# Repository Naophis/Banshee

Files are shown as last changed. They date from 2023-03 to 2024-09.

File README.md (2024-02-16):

# Banshee
 
2022年全日本大会で突貫で2セル化したExiaSnowWhiteをベースに、正式な2セル機として作成したシリーズ。  
ExiaSnowWhiteでは電源周りのノイズに苦戦した反省から回路の見直しを実施。  
足回りについてはマイクロマウス合宿で発表した「ベアリングホルダー方式」を採用することで、足回りの剛性を強化。高速走行時の安定性につなぐことができた機体です。

このリポジトリでは、Bansheeで利用しているすべてのソースコードと基板のファイルを公開しています。

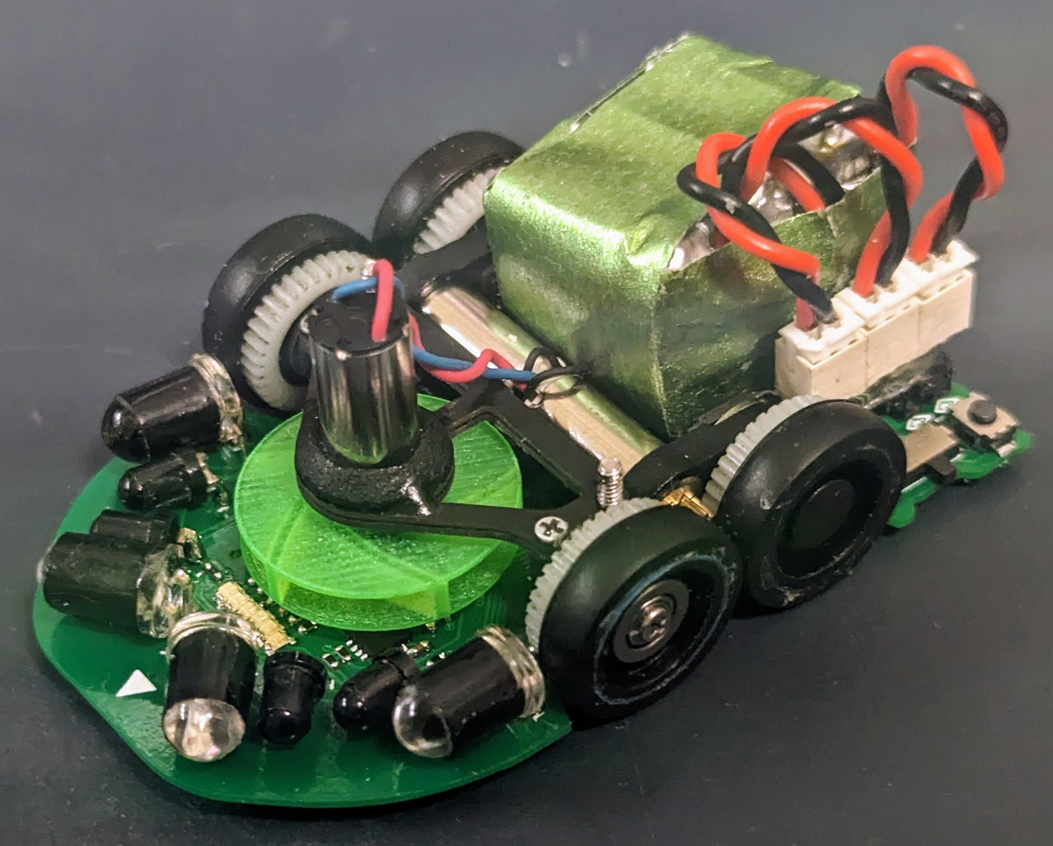
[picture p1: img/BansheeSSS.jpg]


## 利用部品解説

### 1. CPU
ESP32-S3の以下の型番を利用
* ESP32-S3-FH4R2 (Banshee/BansheeAlter)
* ESP32-S3-PICO-1 (Banshee.SSS)

上記の2モデルは昨年発売されておらず、今シーズンから採用。  
昨年使用していたESP32-S3-FN8との違いはPSRAMが搭載で、2MBまでログを取得できるようになったことで細かい解析ができるようになった。

ESP32-PICO-1ではオシレーターの内蔵版となったことで部品点数削減につながった。

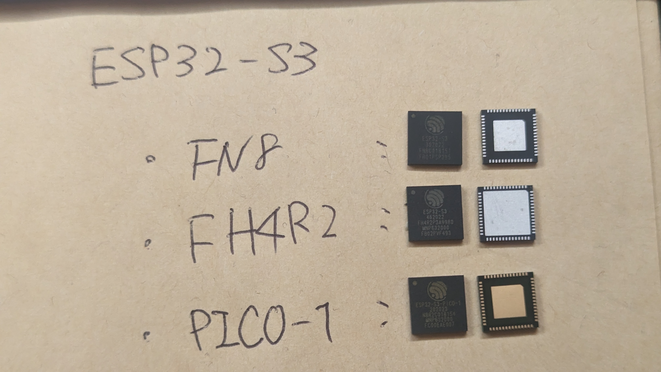
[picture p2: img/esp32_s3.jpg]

画像の通りパッドに違いがある。

#### 1.1 困ったこと
#### 1.1.1 FreeRTOSの固着
ESP32-S3ではデータシートにオシレーターの推奨回路が提示されているが、そのとおり実装すると、モーターを高Dutyで回した際に、FreeRTOSが停止するという問題が発生、推奨回路のコンデンサを除去することで解決した。

#### 1.1.2 データシートにないピンの初期値High問題
書き込み時、電源投入時にHighを出力するピンが存在した。  
ESP32の他シリーズではデータシートに記載しているものもあるがS3では未記載である。
モータードライバにつながったピンに利用すると書き込み時にDuty100%で回転するなど、運用面の問題が発生するため回路の作り直しにつながった。

以下が問題のピン
* PIN26: GPIO20
* PIN28: GPIO26
* PIN44: GPIO39
> 他にもある可能性があり。

### 2. MotorDriver
* DRV8835  (Banshee/BansheeAlter)
* TB6614FNG (Banshee.SSS)

#### 2.1 DRV8835
多くの機体で採用されているが、その理由は以下の通り。
1. 小型ながら2A出力できるため、パフォーマンスが高い。
2. 内部抵抗が300mΩと低い
3. スイッチング周波数が最大250kHzと高く、モーターの特性に対応しやすい。
4. dead timeが100nsecと短いため、高めのPWM周波数に対応しやすい。
dead timeについては、大きい場合High-Lowの切り替えに時間がかかりすぎ、何も出力できないということがあり得る。同社の別のモータードライバでは同じような使い方をするとモーターが回らないということがあり得る。

しかし、最大定格が12Vまでであることから、3セルには対応できないため、TB6614FNGに切り替えた。

### 2.2 TB6614GNG
ディスコン部品であり、パッケージもSOP16と大きいが採用理由は以下の通り。
1. 定格が15Vと3セルに対応
2. 出力が瞬間最大4.5Aまで出力できる
3. スイッチング周波数が400kHzと非常に高く、モーターの特性に対応しやすい
4. dead timeが80nsecと短い

3セル化に伴い、クラシックで利用実績があったICであり、パワー勝負するために信頼できることから採用した。

### 3. PowerSupply
#### 3.1 LXDC55
2セル、3セルから直接3.3Vを取得する場合損失が大きく、熱による影響と効率の観点からDCDCコンバータを採用。入力側に容量が大きいコンデンサをつけないとノイズが乗りやすいため、高分子タンタルコンデンサを複数搭載することでノイズ問題は解決した。

> 約4.2Vを出力するよう、500Ωを利用。  

秋月にて購入できるため採用。

#### 3.2 MIC5319-3.3YM5
3.3V出力に利用。LEDの出力を大きくしたため、500mA出力できるこのICを採用。
データシート通りバイパス用のピンに470pFのコンデンサをつけることでノイズの低減効果がある。

秋月にて購入できるため採用。

### 4. LED + PhotoTransistor
* LED:
  * OSI5FU3A11C
  * VSLY5940
* PhotoTransistor: 
  * LTR-4206E

BCR421UFD（定電流回路）を使うことで安定したセンシングを狙っていたが、
昨年の全日本大会では会場の照明が近いことから、環境ノイズの影響を大きく受けた。  
今年も同じ会場になることから、SN比が良くなるよう、高出力化できる＋LTR-4206Eの帯域に合う大型LEDを採用した

#### 5. gyro
LSM6DSRXTRを採用。4000deg/sec対応している点、昨年のExiaSnowWhiteから継続採用

#### 6. encoder
AS5147Pを採用。14bit対応+28000RPMまで対応しているため継続採用。

ベアリングホルダー方式ではエンコーダ基板に穴を開けることで位置決めしやすいした。

## システム解説

Espressif社がESP32向けにカスタムしたFreeRTOSを利用。  
マイクロマウスでは一定周期で実行したい処理と非同期で実行したい処理が大きく分かれる、これらが混在すると周期に乱れが生じてしまう。ESP32-S3はCPUを2コア搭載していることから、物理的に分けて処理することでシステム全体を滞りなく動かすことを狙った設計となっている。
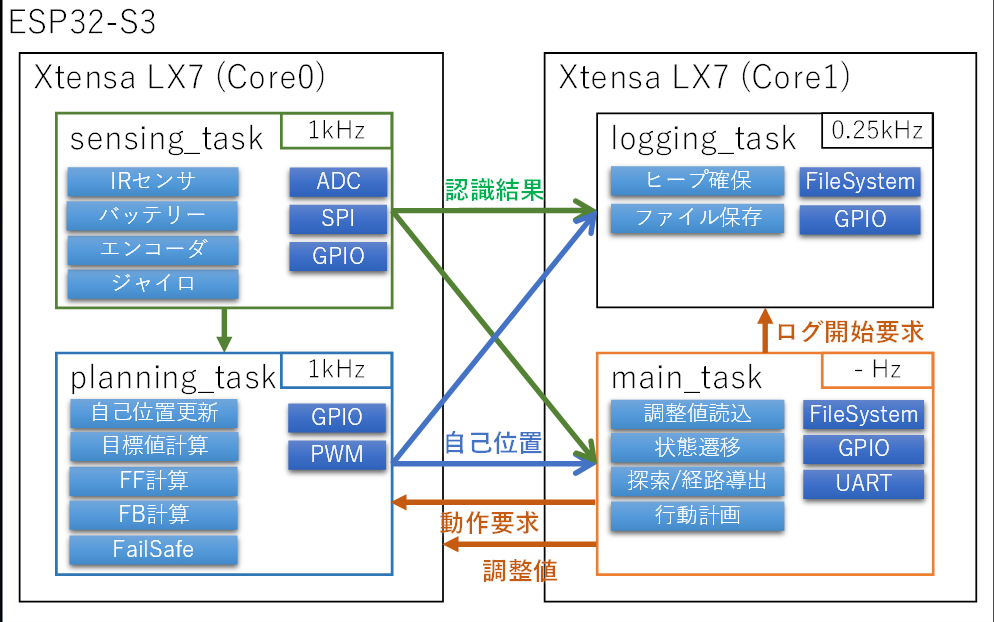
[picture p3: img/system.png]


### 工夫
リアルタイムOSを利用しているとはいえ、タスクの優先順位次第では一定周期で処理できないことがある。特にエンコーダは前回値との差を使い速度を算出するため時刻差の影響を大きく受けた。

対策として、前回取得した時刻を記憶、現在時刻との差分から速度、距離の算出に利用したことで制御・判断の精度向上した。

### 課題
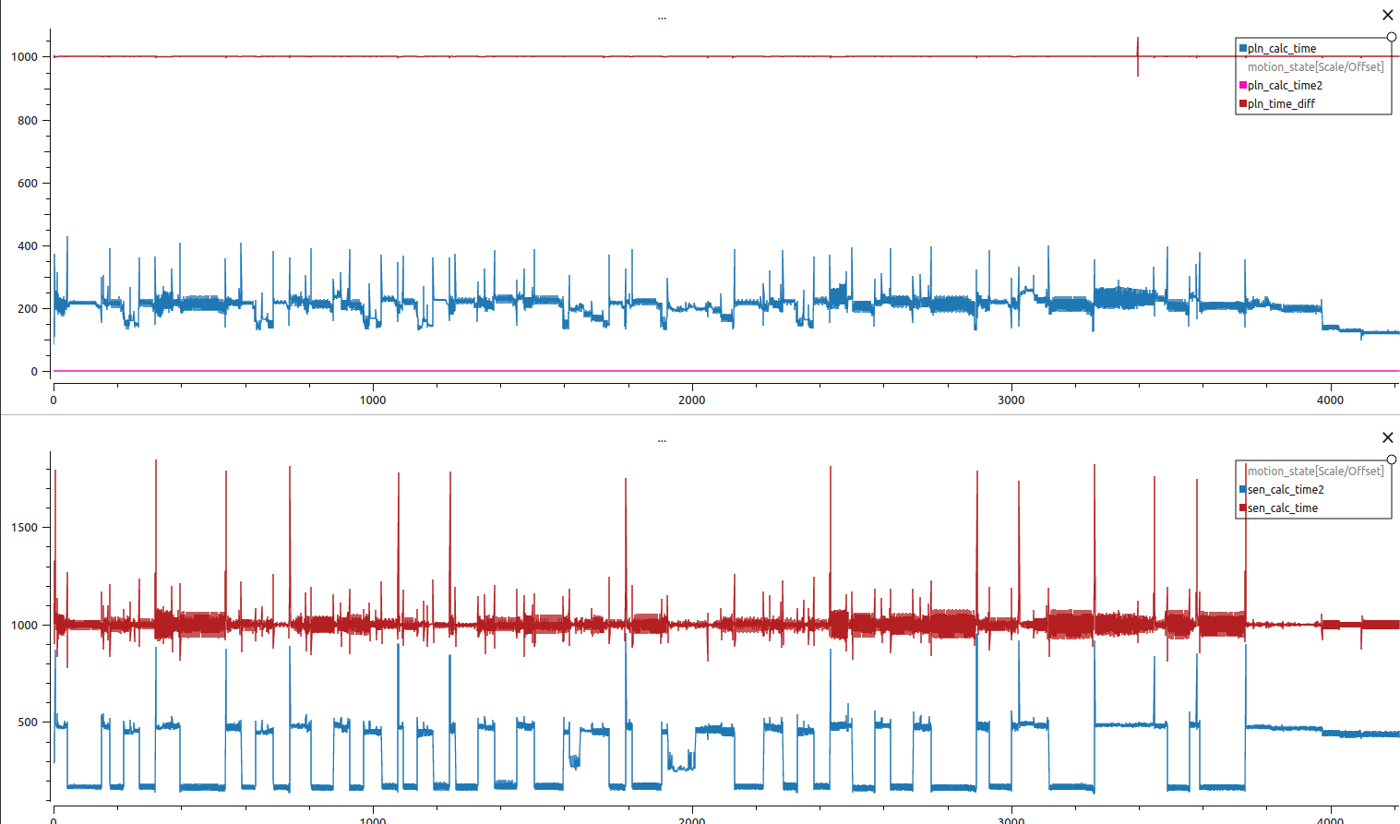
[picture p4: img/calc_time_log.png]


上記の画像は上側がplanning_task、下側がsensing_taskの処理時間(μsec)のログである。  
特にsensing_taskでは、定期的に1000μsecを大きく超え、周期が安定しないときが見られる。
また、planningのタスクの優先度を高く設定しているため、安定しているように見える。

原因は2つ判明しており、  
1つ目はmain_taskから要求される指示メッセージの処理不可が大きい点  
2つ目はセンサーに使用するAD変換に時間がかかる点  
である。

メッセージの送信自体が重くデータは構造体ではなく、ポインタを送信しているためデータ量に起因するものではないため、改善が難しい。
AD変換もESP32自体がIoT向けのマイコンである点からあまり得意でないことから改善が不可能である。

AD変換については、常にすべてのAD変換を行うのではなく、重要度の低いものは１回おきに取得することでシステム全体の負荷を下げるなどの工夫はしているが不十分な状況である。

いずれも今後発売予定のESP32-P4による性能向上に伴う改善を期待する。

## change log
1. Banshee
2. Banshee Alter
3. ~~(BansheeNorn)~~
4. Banshee.SSS　(latest)

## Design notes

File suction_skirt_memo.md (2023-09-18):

* L: 50[mm]
  * front_offset: 10mm
* W: 30[mm]
  * side_offset: 8mm

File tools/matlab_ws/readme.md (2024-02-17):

## Banshee Planning Simulink

BansheeのPlanningではmain_taskから要求された目標値(位置、角度)と制約(速度、加速度、角加速度など)をもとに指令値を算出するロジックをMatlab/Simulinkで実装しています。



## How to use

matlab_wsにて、`include`、`model`、`src`をサブフォルダを含めpathに追加し、`init.m`を実行。Figureが出たら完了。

`sim_mpc.slx`を開き実行すると、`init.m`で宣言した目標値をベースに指令値を算出するシミュレーションを実行する

モードは`init.m`のtest_modeで制御している（書き換えたら都度`init`を実行する必要あり）また、test_modeのコードを直接変更必要がある。

以下がモードです。
0. 直進
1. スラローム（オリジナル加速）
2. 超信地旋回
3. 後退
4. スラローム（固定加速度）

init後はsim_mpc.slxで実行し、各種速度、角速度などの指示値がどうなっているかscopeで確認する

## how to integration

`build_mpc_tgt_calc.m`を実行するとEmmbedd coderでコード生成し所定のフォルダに出力する。Bansheeではこのコードを参照、ビルドしやすいよう、シンボリックリンクにて参照関係を解決している。

## issue

`mpc_tgt_calc.slx`のIf1ブロックにて判断されるロジックが生成するコードにおいて、以下のコンパイルエラーとなるものが生成される。

```log
/home/naoto/Desktop/mouse/Banshee/main/gen_code_mpc/mpc_tgt_calc.cpp:584:40: error: suggest parentheses around '&&' within '||' [-Werror=parentheses]
  583 |   if (arg_mode == mpc_tgt_calc_P.Constant_Value_k || arg_mode ==
      |                                                      ~~~~~~~~~~~
  584 |       mpc_tgt_calc_P.Constant3_Value_i && (rtb_RelationalOperator1_g0 &&
      |       ~~~~~~~~~~~~~~~~~~~~~~~~~~~~~~~~~^~~~~~~~~~~~~~~~~~~~~~~~~~~~~~~~~
  585 |        rtb_NOT2)) {
      |        ~~~~~~~~~     
```

原因は&&と||を組み合わせて利用しているif文において、その優先順位が明確でないことによるものである。

コンパイラオプションで回避可能であるものの、明確な優先順位をつけないとコンパイラ次第で挙動が変わり得るものであることは確かである。

以下のように()を入れることで成立する。
```cpp
  if (arg_mode == mpc_tgt_calc_P.Constant_Value_k || (arg_mode ==
      mpc_tgt_calc_P.Constant3_Value_i && (rtb_RelationalOperator1_g0 &&
       rtb_NOT2))) {
```

> （流石にこれはコード生成上のガバでは？）

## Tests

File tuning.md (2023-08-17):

# 調整

## 基本機能確認
* UI(ボタン)確認
  * GPIO
* UI(LED)確認
  * I2C
* UI(ブザー)確認
  * PWM(LED PWM)
* ADCポート対応確認
  * バッテリー
  * LEDセンサー
* 駆動モーター左右PWM確認
  * Motor PWM
* 駆動モーターCW/CCW確認
  * GPIO
* 吸引モーター確認
  * Motor PWM

## 単体機能の調整
* センサーLED発光時間調整
  * `led_light_delay_cnt`をセンサー値が上がりきるまで長くする
  * mode:14
* センサー曲線フィッティング
  * mode:15 + ./csv/sensor.sh
* 駆動モーター PWM周波数調整
  * mode:13, mode:2, mode:3
* 吸引モーター　PWM周波数調整
  * mode:11

## ゲイン調整
* 速度制御
  * mode:13, 2
* 角速度制御
  * mode:13, 3
* LEDセンサー制御
  * mode:2 (斜めは後で)

## 単体機能調整
* LEDセンサーと壁との距離オフセット調整
  * mode:2 
* タイヤ径調整
  * mode:2
  * できるだけ長い距離でテスト
* 前壁制御調整: search.exist
  * mode:7
  * 反応距離閾値：`front_ctrl_th`
  * ref距離：`front_ctrl`
  * 角度オフセット: `kireme_r` 負の値で左にオフセットする
  * 前壁制御DutyMAX値： `offset_l`
  * [終了条件]前壁と偏差許容値: `kireme_l`
  * [終了条件]前壁との傾き許容偏差: `offset_r`
* 探索時壁切れ考慮位置調整
  * mode:2 (片側の壁制御を切りながら)
  * `clear_dist_ragne_from`
  * `clear_dist_ragne_to`
* 探索前壁調整：
  * mode:5
  * `front_dist_offset`
* 角速度ゲイン調整
  * mode:3
* FF調整
  * mode:2, 3
* 壁切れ調整
  * 
* 探索スラローム
  * 左右壁オフセットref: `sla_wall_ref_l`/`sla_wall_ref_r`

  * 探索前壁位置調整: 

## テスト

### 探索テスト

###

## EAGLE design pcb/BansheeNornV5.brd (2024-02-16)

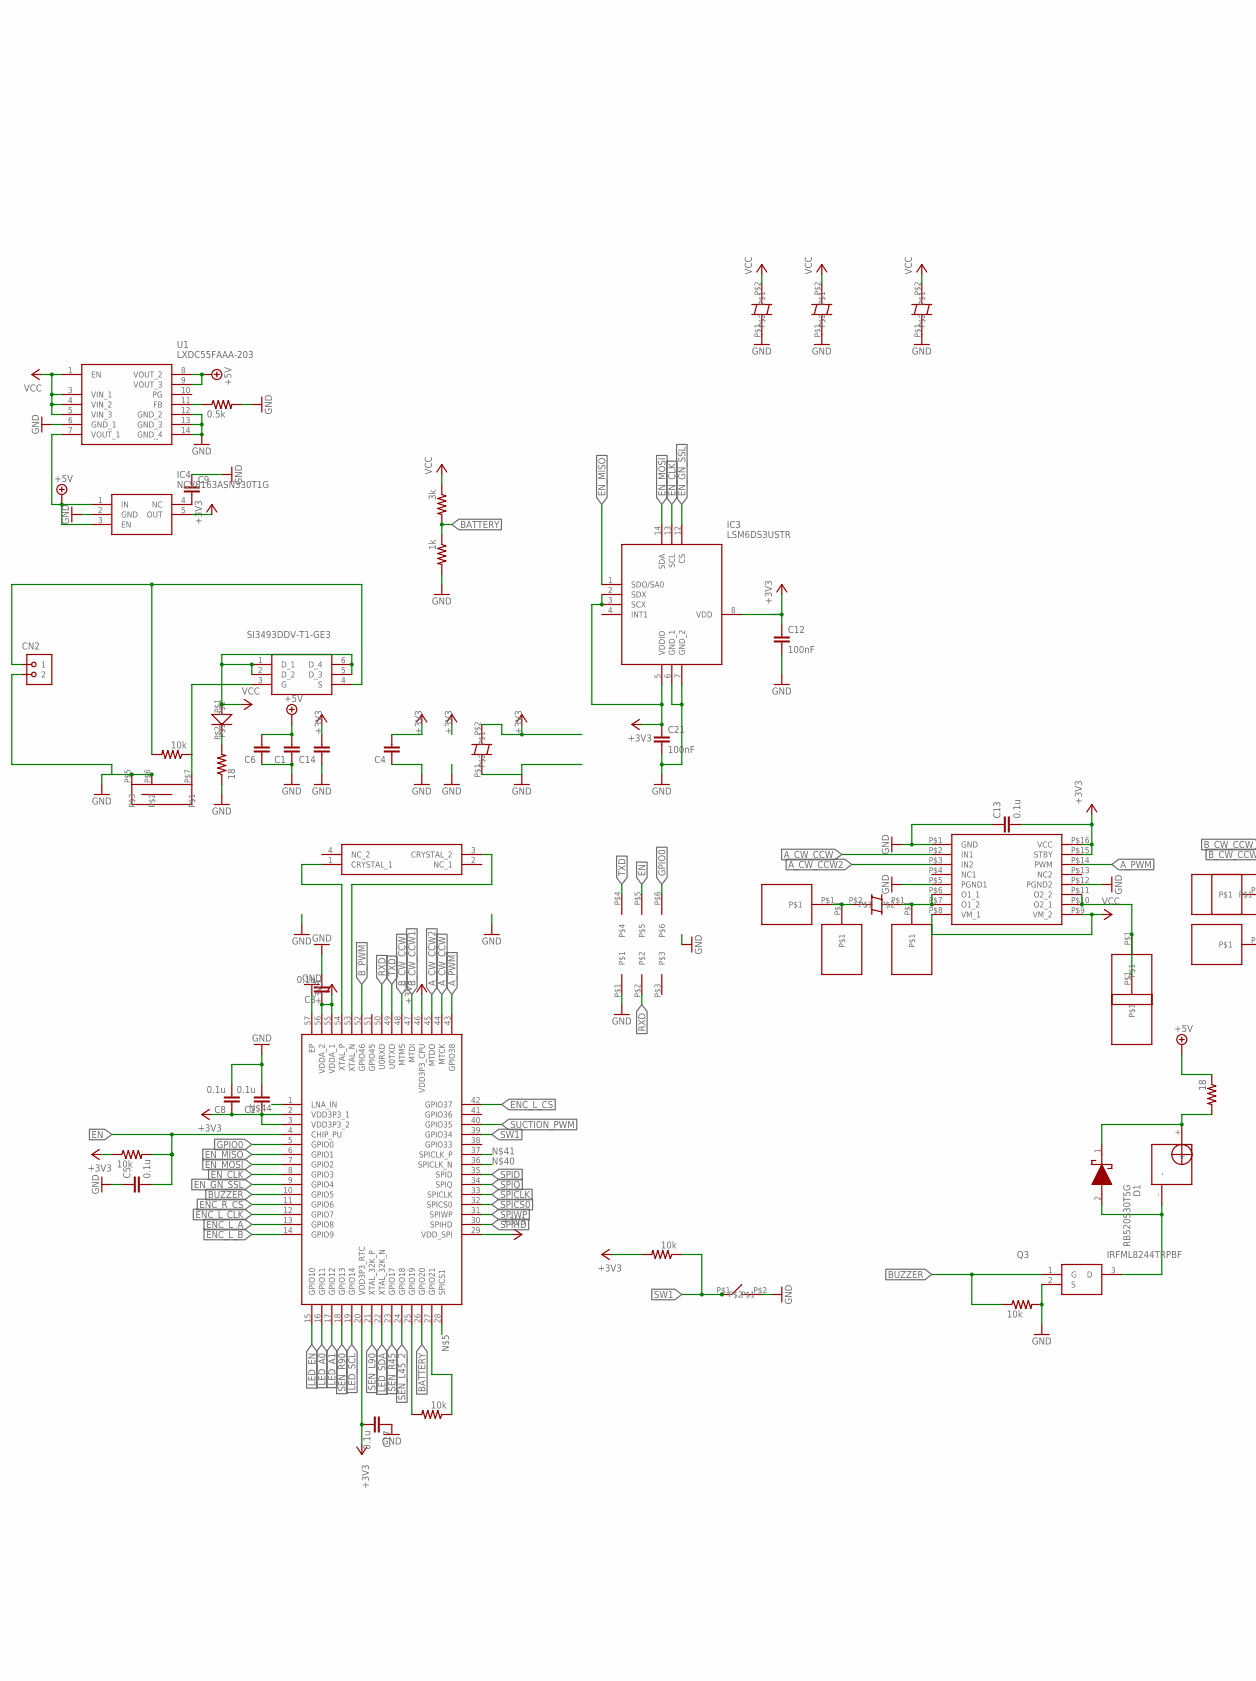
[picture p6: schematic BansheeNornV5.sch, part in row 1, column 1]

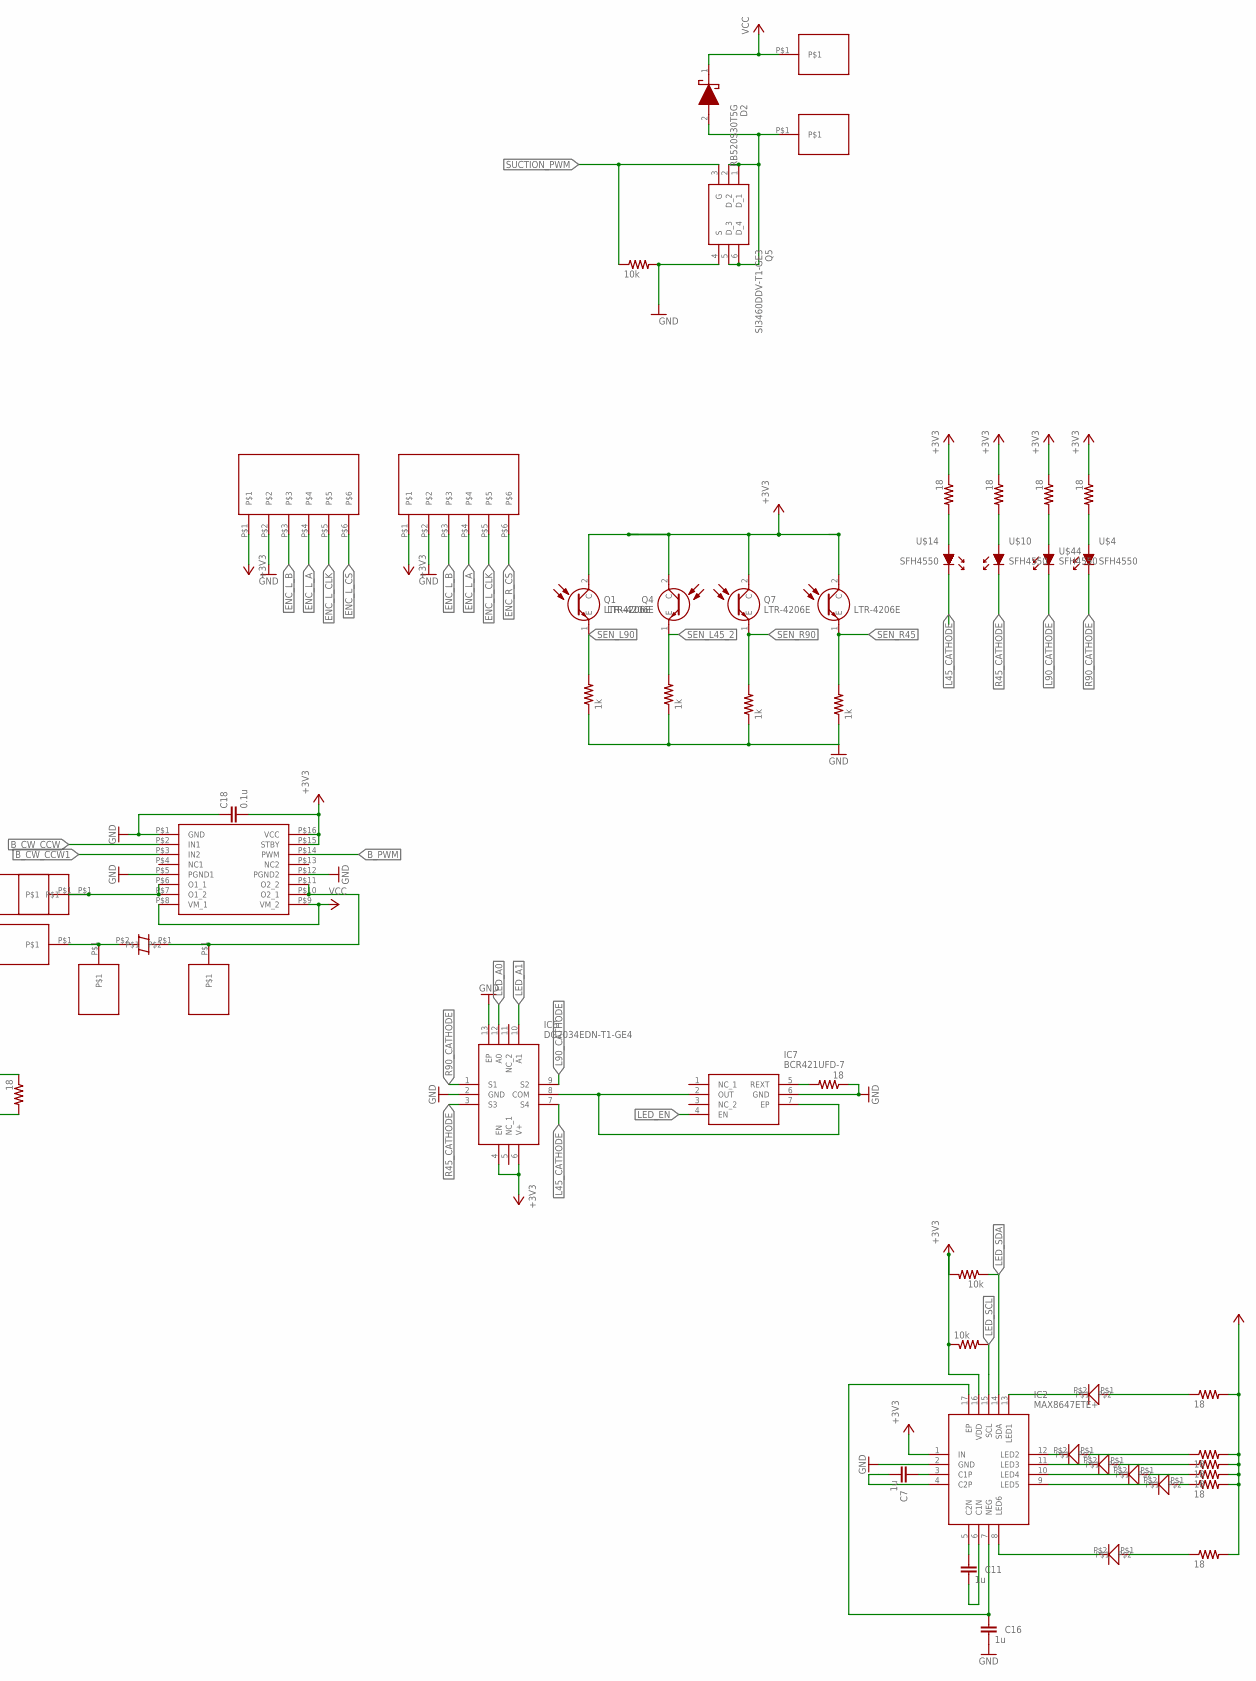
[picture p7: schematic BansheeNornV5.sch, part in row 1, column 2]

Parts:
C1, C4, C6, C14: C3216
C2, C3, C5, C8, C13, C17, C18: 0.1u; R1005
C7, C11, C16: 1u; R1005
C9: C1608
C12, C21: 100nF; R1005
CN2: HRCON-2
D1, D2: RB520S30T5G; SODFL1608X70N
IC1: ESP32-S3-WROOM-1-N8; QFN40P700X700X90-57N
IC2: MAX8647ETE+; QFN50P300X300X80-17N
IC3: LSM6DS3USTR; LGA-14(2.5X3X0.86)
IC4: NCV8163ASN330T1G; SOT95P275X110-5N
IC6: DG2034EDN-T1-GE4; QFN50P300X300X100-13N
IC7: BCR421UFD-7; BCR421UFD7
Q1, Q4, Q7, Q8: LTR-4206E; LTR4206E
Q2: SI3493DDV-T1-GE3; SOT95P284X110-6N
Q3: IRFML8244TRPBF; SOT95P237X112-3N
Q5: SI3460DDV-T1-GE3; SOT95P284X110-6N
R1, R4, R7, R8, R9, R12, R13, R21: 10k; R1005
R2: 3k; R1005
R3, R16, R17, R18, R22: 1k; R1005
R5: 0.5k; R1005
R6, R10, R15, R19, R25, R26, R27, R28, R29, R30, R31, R32, R33: 18; R1608
U1: LXDC55FAAA-203; LXDC55FAAA203
U$1, U$8, U$9, U$11, U$17, U$20, U$26, U$27, U$29, U$32, U$57, U$58: PAD
U$2, U$19, U$21, U$23, U$25, U$30, U$31: LED_1005
U$3, U$5, U$7, U$12, U$16, U$24: PANA
U$4, U$10, U$14, U$44: SFH4550; SFH_4550
U$6: PIN2_3
U$13: BUZZER_44; BUZZER
U$15, U$28: ENCORDER_1; ENCORDER_R
U$18, U$22: TB6614
U$43: TVAF06
U$53: SWICH; SWITCH
Y1: XRCGB40M000F5A00R0; XRCGB32_F

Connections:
+3V3: C2.P$1 (1), C3.P$1 (1), C4.2, C8.P$1 (1), C12.P$1 (1), C13.P$2 (2), C14.2, C17.P$2 (2), C18.P$2 (2), C21.P$1 (1), IC1.2 (VDD3P3_1), IC1.3 (VDD3P3_2), IC1.20 (VDD3P3_RTC), IC1.29 (VDD_SPI), IC1.46 (VDD3P3_CPU), IC1.55 (VDDA_1), IC1.56 (VDDA_2), IC2.1 (IN), IC2.16 (VDD), IC3.2 (SDX), IC3.3 (SCX), IC3.5 (VDDIO), IC3.8 (VDD), IC4.5 (OUT), IC6.4 (EN), IC6.6 (V+), Q1.2 (C), Q4.2 (C), Q7.2 (C), Q8.2 (C), R1.P$1 (1), R8.P$2 (2), R12.P$1 (1), R13.P$2 (2), R15.1, R25.1, R26.1, R27.2, R28.2, R29.1, R30.2, R31.2, R32.2, R33.2, U$15.P$1, U$18.P$15 (STBY), U$18.P$16 (VCC), U$22.P$15 (STBY), U$22.P$16 (VCC), U$24.P$2, U$28.P$1
+5V: C1.2, C6.2, IC4.1 (IN), IC4.3 (EN), R10.1, U1.7 (VOUT_1), U1.8 (VOUT_2), U1.9 (VOUT_3)
A_CW_CCW: IC1.44 (MTCK), U$18.P$2 (IN1)
A_CW_CCW2: IC1.45 (MTDO), U$18.P$3 (IN2)
A_PWM: IC1.43 (GPIO38), U$18.P$14 (PWM)
BATTERY: IC1.26 (GPIO20), R2.P$2 (2), R3.P$1 (1)
BUZZER: IC1.10 (GPIO5), Q3.1 (G), R9.P$1 (1)
B_CW_CCW: IC1.48 (MTMS), U$22.P$2 (IN1)
B_CW_CCW1: IC1.47 (MTDI), U$22.P$3 (IN2)
B_PWM: IC1.52 (GPIO46), U$22.P$14 (PWM)
EN: C5.P$2 (2), IC1.4 (CHIP_PU), R1.P$2 (2), U$6.P$5
ENC_L_A: IC1.13 (GPIO8), U$15.P$4, U$28.P$4
ENC_L_B: IC1.14 (GPIO9), U$15.P$3, U$28.P$3
ENC_L_CLK: IC1.12 (GPIO7), U$15.P$5, U$28.P$5
ENC_L_CS: IC1.42 (GPIO37), U$15.P$6
ENC_R_CS: IC1.11 (GPIO6), U$28.P$6
EN_CLK: IC1.8 (GPIO3), IC3.13 (SCL)
EN_GN_SSL: IC1.9 (GPIO4), IC3.12 (CS)
EN_MISO: IC1.6 (GPIO1), IC3.1 (SDO/SA0)
EN_MOSI: IC1.7 (GPIO2), IC3.14 (SDA)
GND: C1.1, C2.P$2 (2), C3.P$2 (2), C4.1, C5.P$1 (1), C6.1, C8.P$2 (2), C9.1, C12.P$2 (2), C13.P$1 (1), C14.1, C16.P$2 (2), C17.P$1 (1), C18.P$1 (1), C21.P$2 (2), CN2.2, IC1.57 (EP), IC2.2 (GND), IC3.6 (GND_1), IC3.7 (GND_2), IC4.2 (GND), IC6.2 (GND), IC6.13 (EP), IC7.6 (GND), Q3.2 (S), Q5.4 (S), R3.P$2 (2), R5.P$2 (2), R6.1, R9.P$2 (2), R16.P$1 (1), R17.P$1 (1), R18.P$1 (1), R19.1, R21.P$2 (2), R22.P$1 (1), U1.6 (GND_1), U1.12 (GND_2), U1.13 (GND_3), U1.14 (GND_4), U$5.P$1, U$6.P$1, U$12.P$1, U$15.P$2, U$16.P$1, U$18.P$1 (GND), U$18.P$5 (PGND1), U$18.P$12 (PGND2), U$22.P$1 (GND), U$22.P$5 (PGND1), U$22.P$12 (PGND2), U$24.P$1, U$28.P$2, U$43.P$2, U$53.P$5, U$53.P$6
GPIO0: IC1.5 (GPIO0), U$6.P$6
L45_CATHODE: IC6.7 (S4), U$14.CASODE (K)
L90_CATHODE: IC6.9 (S2), U$44.CASODE (K)
LED_A0: IC1.16 (GPIO11), IC6.12 (A0)
LED_A1: IC1.17 (GPIO12), IC6.10 (A1)
LED_EN: IC1.15 (GPIO10), IC7.4 (EN)
LED_SCL: IC1.19 (GPIO14), IC2.15 (SCL), R12.P$2 (2)
LED_SDA: IC1.22 (XTAL_32K_N), IC2.14 (SDA), R13.P$1 (1)
unnamed: D1.1 (K), R10.2, U$13.+
unnamed: IC6.8 (COM), IC7.2 (OUT), IC7.7 (EP)
unnamed: D1.2 (A), Q3.3 (D), U$13.-
unnamed: R6.2, U$2.P$2
unnamed: U$3.P$1, U$9.P$1, U$18.P$6 (O1_1), U$18.P$7 (O1_2)
unnamed: R33.1, U$30.P$1
unnamed: R32.1, U$23.P$1
unnamed: R31.1, U$21.P$1
unnamed: R30.1, U$19.P$1
unnamed: R28.1, U$25.P$1
unnamed: IC1.25 (GPIO19), R4.P$2 (2)
unnamed: U$7.P$1, U$17.P$1, U$22.P$10 (O2_1), U$22.P$11 (O2_2)
unnamed: R27.1, U$31.P$1
unnamed: Q2.3 (G), R7.P$1 (1), U$53.P$7
unnamed: C9.2, IC4.4 (NC)
unnamed: CN2.1, Q2.4 (S), R7.P$2 (2)
unnamed: R29.2, U$14.ANODE (A)
unnamed: R15.2, U$10.ANODE (A)
unnamed: R25.2, U$44.ANODE (A)
unnamed: R26.2, U$4.ANODE (A)
unnamed: IC1.27 (GPIO21), R4.P$1 (1)
unnamed: U$3.P$2, U$11.P$1, U$27.P$1
unnamed: U$7.P$2, U$26.P$1, U$57.P$1
unnamed: IC7.5 (REXT), R19.2
unnamed: R5.P$1 (1), U1.11 (FB)
unnamed: D2.2 (A), Q5.1 (D_1), Q5.2 (D_2), Q5.5 (D_3), Q5.6 (D_4), U$58.P$1
unnamed: IC1.54 (XTAL_P), Y1.1 (CRYSTAL_1)
unnamed: IC1.53 (XTAL_N), Y1.3 (CRYSTAL_2)
unnamed: U$1.P$1, U$18.P$10 (O2_1), U$18.P$11 (O2_2), U$32.P$1
unnamed: U$8.P$1, U$22.P$6 (O1_1), U$22.P$7 (O1_2), U$29.P$1
unnamed: C7.P$1 (1), IC2.3 (C1P)
unnamed: C7.P$2 (2), IC2.4 (C2P)
unnamed: C11.P$1 (1), IC2.5 (C2N)
unnamed: C11.P$2 (2), IC2.6 (C1N)
unnamed: C16.P$1 (1), IC2.7 (NEG), IC2.17 (EP)
unnamed: IC2.8 (LED6), U$31.P$2
unnamed: IC2.13 (LED1), U$30.P$2
unnamed: IC2.12 (LED2), U$23.P$2
unnamed: IC2.11 (LED3), U$21.P$2
unnamed: IC2.10 (LED4), U$19.P$2
unnamed: IC2.9 (LED5), U$25.P$2
R45_CATHODE: IC6.3 (S3), U$10.CASODE (K)
R90_CATHODE: IC6.1 (S1), U$4.CASODE (K)
RXD: IC1.50 (U0RXD), U$6.P$2
SEN_L45_2: IC1.24 (GPIO18), Q4.1 (E), R17.P$2 (2)
SEN_L90: IC1.21 (XTAL_32K_P), Q1.1 (E), R18.P$2 (2)
SEN_R45: IC1.23 (GPIO17), Q8.1 (E), R16.P$2 (2)
SEN_R90: IC1.18 (GPIO13), Q7.1 (E), R22.P$2 (2)
SPICLK: IC1.33 (SPICLK)
SPICS0: IC1.32 (SPICS0)
SPID: IC1.35 (SPID)
SPIHD: IC1.30 (SPIHD)
SPIQ: IC1.34 (SPIQ)
SPIWP: IC1.31 (SPIWP)
SUCTION_PWM: IC1.40 (GPIO35), Q5.3 (G), R21.P$1 (1)
SW1: IC1.39 (GPIO34), R8.P$1 (1), U$43.P$1
TXD: IC1.49 (U0TXD), U$6.P$4
VCC: D2.1 (K), Q2.1 (D_1), Q2.2 (D_2), Q2.5 (D_3), Q2.6 (D_4), R2.P$1 (1), U1.1 (EN), U1.3 (VIN_1), U1.4 (VIN_2), U1.5 (VIN_3), U$2.P$1, U$5.P$2, U$12.P$2, U$16.P$2, U$18.P$8 (VM_1), U$18.P$9 (VM_2), U$20.P$1, U$22.P$8 (VM_1), U$22.P$9 (VM_2)

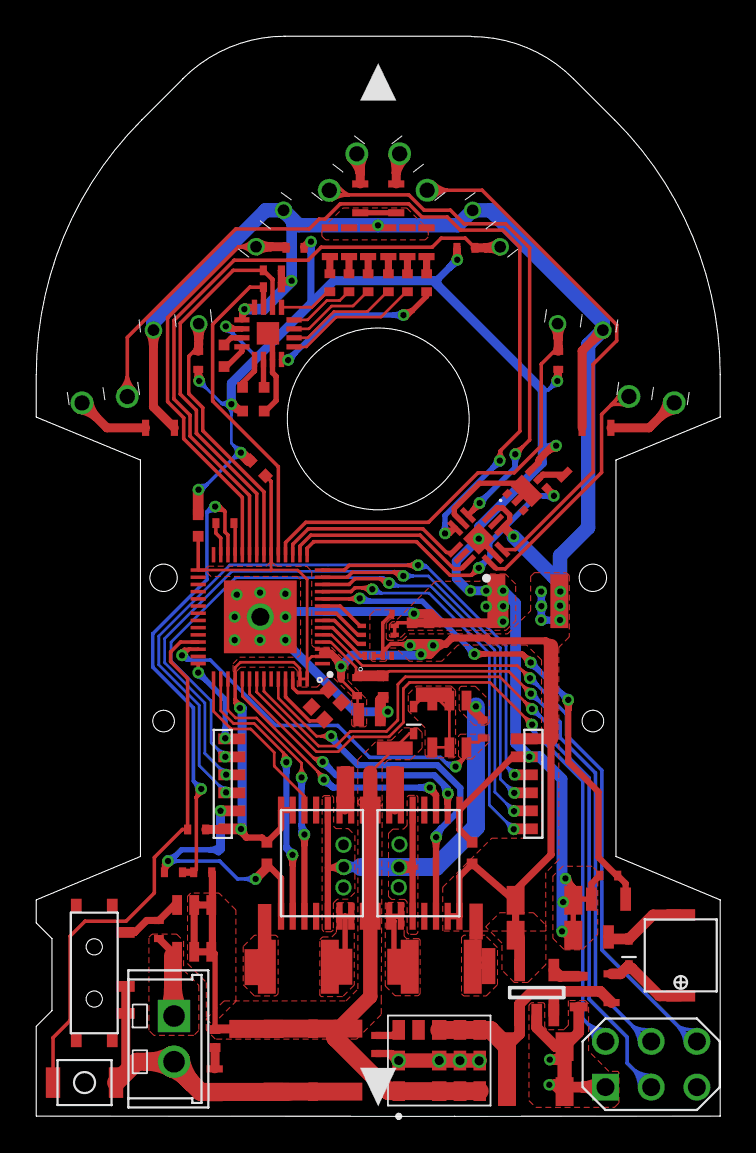
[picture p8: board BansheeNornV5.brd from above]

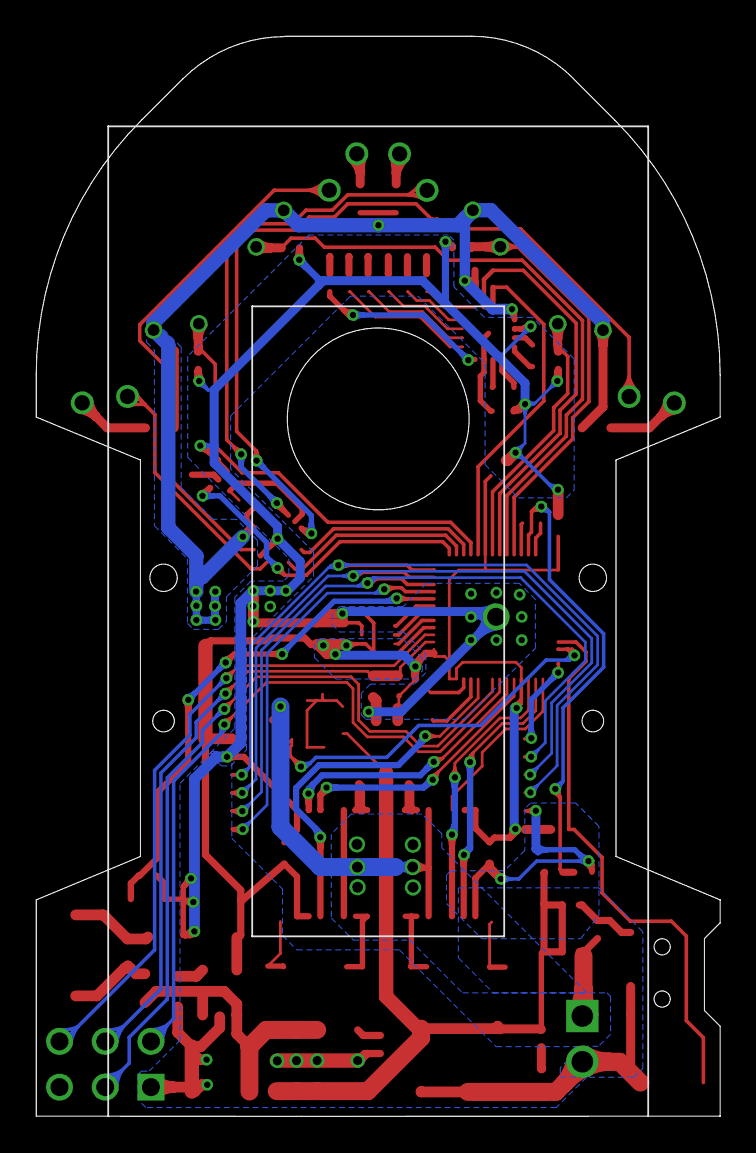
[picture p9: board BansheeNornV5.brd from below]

Board: 2 copper layers, 38.0 x 60.0 mm, 100 parts (2 on the bottom side), 81 nets.

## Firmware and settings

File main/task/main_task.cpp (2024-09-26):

#include "include/main_task.hpp"

#define getItem cJSON_GetObjectItem
#define getArray cJSON_GetArrayItem
MainTask::MainTask() {
  ui = std::make_shared<UserInterface>();
  mp = std::make_shared<MotionPlanning>();
  lgc = std::make_shared<MazeSolverBaseLgc>();
  search_ctrl = std::make_shared<SearchController>();
  pc = std::make_shared<PathCreator>();
  mp->set_path_creator(pc);
}

MainTask::~MainTask() {}

void MainTask::create_task(const BaseType_t xCoreID) {
  // xTaskCreatePinnedToCore(task_entry_point, "main_task", 8192, this, 2, th,
  //                         xCoreID);
  xTaskCreatePinnedToCore(task_entry_point, "main_task", 8192, this, 2, NULL,
                          xCoreID);
}
void MainTask::task_entry_point(void *task_instance) {
  static_cast<MainTask *>(task_instance)->task();
}
void MainTask::set_sensing_entity(
    std::shared_ptr<sensing_result_entity_t> &_sensing_result) {
  sensing_result = _sensing_result;
  ui->set_sensing_entity(_sensing_result);
  ui->init_i2c_master();
  mp->set_sensing_entity(_sensing_result);
  search_ctrl->set_sensing_entity(_sensing_result);
}
void MainTask::set_input_param_entity(std::shared_ptr<input_param_t> &_param) {
  param = _param;
  mp->set_input_param_entity(_param);
  search_ctrl->set_input_param_entity(_param);
}
void MainTask::set_tgt_val(std::shared_ptr<motion_tgt_val_t> &_tgt_val) {
  tgt_val = _tgt_val;
  ui->set_tgt_val(_tgt_val);
  mp->set_tgt_val(_tgt_val);
}
void MainTask::set_planning_task(std::shared_ptr<PlanningTask> &_pt) {
  pt = _pt;
  search_ctrl->set_planning_task(_pt);
  mp->set_planning_task(_pt);
}
void MainTask::set_logging_task(std::shared_ptr<LoggingTask> &_lt) {
  lt = _lt; //
  search_ctrl->set_logging_task(lt);
  mp->set_logging_task(lt);
}
void MainTask::check_battery() {
  vTaskDelay(1500.0 / portTICK_PERIOD_MS); //他モジュールの起動待ち

  printf("battery= %f\n", sensing_result->ego.battery_raw);
  if (sensing_result->ego.battery_raw > LOW_BATTERY_TH ||
      sensing_result->ego.battery_raw < 9.5)
    return;
  while (1) {
    ui->music_sync(MUSIC::G5_, 250);
    vTaskDelay(tgt_val->buzzer.time / portTICK_PERIOD_MS);
    bool break_btn = ui->button_state_hold();
    if (break_btn) {
      ui->coin(100);
      break;
    }
  }
}

TurnType MainTask::cast_turn_type(std::string str) {
  if (str == "normal")
    return TurnType::Normal;
  if (str == "large")
    return TurnType::Large;
  if (str == "orval")
    return TurnType::Orval;
  if (str == "dia45")
    return TurnType::Dia45;
  if (str == "dia45_2")
    return TurnType::Dia45_2;
  if (str == "dia135")
    return TurnType::Dia135;
  if (str == "dia135_2")
    return TurnType::Dia135_2;
  if (str == "dia90")
    return TurnType::Dia90;
  return TurnType::None;
}
void IRAM_ATTR MainTask::dump1() {
  notify_handle = xTaskGetCurrentTaskHandle();
  mp->reset_gyro_ref_with_check();
  tgt_val->nmr.motion_type = MotionType::SENSING_DUMP;
  tgt_val->nmr.timstamp++;

  xTaskNotify(*th, (uint32_t)tgt_val.get(), eSetValueWithOverwrite);
  while (1) {

    printf("%c[2J", ESC);   /* 画面消去 */
    printf("%c[0;0H", ESC); /* 戦闘戻す*/

    if (ulTaskNotifyTake(pdTRUE, pdMS_TO_TICKS(1))) {
      printf("notification recieve\n");
    }

    printf("SW1 %d \n", gpio_get_level(SW1));

    printf("gyro: %d\t(%0.3f)\n", sensing_result->gyro.raw,
           tgt_val->gyro_zero_p_offset);
    printf("accel_x: %f\t(%f)\n", sensing_result->ego.accel_x_raw,
           sensing_result->ego.accel_x_raw / 9806.65 *
               param->accel_x_param.gain);
    // printf("accel_y: %d\n", sensing_result->accel_y.raw);
    printf("battery: %0.3f (%d)\n", sensing_result->ego.battery_lp,
           sensing_result->battery.raw);
    printf("encoder: %ld, %ld\n", sensing_result->encoder.left,
           sensing_result->encoder.right);
    printf(
        "sensor: %4d, %4d, %4d, %4d, %4d, %4d, %4d\n",
        sensing_result->led_sen.left90.raw, sensing_result->led_sen.left45.raw,
        sensing_result->led_sen.left45_2.raw, sensing_result->led_sen.front.raw,
        sensing_result->led_sen.right45_2.raw,
        sensing_result->led_sen.right45.raw,
        sensing_result->led_sen.right90.raw);
    printf("sensor_before: %4d, %4d, %4d, %4d, %4d\n",
           sensing_result->led_sen_before.left90.raw,
           sensing_result->led_sen_before.left45.raw,
           sensing_result->led_sen_before.front.raw,
           sensing_result->led_sen_before.right45.raw,
           sensing_result->led_sen_before.right90.raw);
    printf("sensor_after: %4d, %4d, %4d, %4d, %4d\n",
           sensing_result->led_sen_after.left90.raw,
           sensing_result->led_sen_after.left45.raw,
           sensing_result->led_sen_after.front.raw,
           sensing_result->led_sen_after.right45.raw,
           sensing_result->led_sen_after.right90.raw);
    printf("sensor_dist(near): %3.2f, %3.2f, %3.2f, %3.2f, %3.2f\n",
           sensing_result->ego.left90_dist,  //
           sensing_result->ego.left45_dist,  //
           sensing_result->ego.front_dist,   //
           sensing_result->ego.right45_dist, //
           sensing_result->ego.right90_dist);
    printf("sensor_dist(mid): %3.2f, %3.2f, %3.2f, %3.2f, %3.2f\n",
           sensing_result->ego.left90_mid_dist, //
           sensing_result->ego.left45_dist,     //
           sensing_result->ego.front_mid_dist,  //
           sensing_result->ego.right45_dist,    //
           sensing_result->ego.right90_mid_dist);
    printf("sensor_dist(far): %3.2f, %3.2f, %3.2f, %3.2f, %3.2f\n",
           sensing_result->ego.left90_far_dist, //
           sensing_result->ego.left45_dist,     //
           sensing_result->ego.front_far_dist,  //
           sensing_result->ego.right45_dist,    //
           sensing_result->ego.right90_far_dist);

    printf("sensor: %0.1f, %0.1f, %0.1f, %0.1f, %0.1f\n",
           param->sen_ref_p.search_exist.left90,
           param->sen_ref_p.search_exist.left45,
           param->sen_ref_p.search_exist.front,
           param->sen_ref_p.search_exist.right45,
           param->sen_ref_p.search_exist.right90);

    printf("ego_v: %4.3f, %4.3f, %4.3f, %4.3f, (%4ld, %4ld)\n",
           sensing_result->ego.v_l, sensing_result->ego.v_c,
           sensing_result->ego.v_r, tgt_val->ego_in.dist,
           sensing_result->encoder.left, sensing_result->encoder.right);

    printf("calc_v: %4.3f, %3.3f\n", tgt_val->ego_in.v, tgt_val->ego_in.w);

    printf("ego_w: %2.3f, %2.3f, %2.3f, %3.3f deg\n", sensing_result->ego.w_raw,
           sensing_result->ego.w_lp, tgt_val->ego_in.ang,
           tgt_val->ego_in.ang * 180 / m_PI);

    printf("gyro_raw[]: %4d, %4d, %4d, %4d, %4d\n",
           sensing_result->gyro_list[0], sensing_result->gyro_list[1],
           sensing_result->gyro_list[2], sensing_result->gyro_list[3],
           sensing_result->gyro_list[4]);

    const float tgt_gain =
        1000.0 /
        (sensing_result->accel_x.raw - tgt_val->accel_x_zero_p_offset) * 9.8;
    printf("accel: %3.3f, %6.6f\n", sensing_result->ego.accel_x_raw, tgt_gain);

    // printf("duty: %3.3f, %3.3f\n", sensing_result->ego.duty.duty_l,
    //        sensing_result->ego.duty.duty_r);

    printf("planning_time: %d\n", tgt_val->calc_time);
    printf("planning_time_diff: %d\n", tgt_val->calc_time_diff);
    printf("sensing_time: %d\n", sensing_result->calc_time);

    if (ui->button_state()) {
      tgt_val->ego_in.ang = tgt_val->ego_in.dist = 0;
    }

    vTaskDelay(xDelay100);
  }
}

void MainTask::dump2() {
  notify_handle = xTaskGetCurrentTaskHandle();
  mp->reset_gyro_ref_with_check();
  tgt_val->nmr.motion_type = MotionType::SENSING_DUMP;
  tgt_val->nmr.timstamp++;

  xTaskNotify(*th, (uint32_t)tgt_val.get(), eSetValueWithOverwrite);

  while (1) {
    printf("%d, %d, %d, %d, %d\n", sensing_result->led_sen.left90.raw,
           sensing_result->led_sen.left45.raw,
           sensing_result->led_sen.front.raw,
           sensing_result->led_sen.right45.raw,
           sensing_result->led_sen.right90.raw);

    if (ui->button_state()) {
      tgt_val->ego_in.ang = tgt_val->ego_in.dist = 0;
    }

    vTaskDelay(xDelay100);
  }
}

int MainTask::select_mode() {
  int mode_num = 0;
  lbit.byte = 0;
  while (1) {
    int res = ui->encoder_operation();
    mode_num += res;
    if (mode_num == -1) {
      mode_num = 16;
    } else if (mode_num == 17) {
      mode_num = (int)(MODE::SEARCH);
    }
    lbit.byte = mode_num + 1;
    ui->LED_bit(lbit.b0, lbit.b1, lbit.b2, lbit.b3, lbit.b4, lbit.b5);
    if (ui->button_state_hold()) {
      ui->coin(100);
      break;
    }
    vTaskDelay(xDelay1);
  }
  return mode_num;
}

void MainTask::reset_tgt_data() { mp->reset_tgt_data(); }

void MainTask::reset_ego_data() { mp->reset_ego_data(); }

void MainTask::keep_pivot() {
  mp->reset_gyro_ref_with_check();
  reset_tgt_data();
  reset_ego_data();
  req_error_reset();
  pt->motor_enable();
  req_error_reset();
  ps.v_max = 0.000000001;
  ps.v_end = 0.000000001;
  ps.dist = 1000;
  ps.accl = 0.1;
  ps.decel = -1;
  ps.sct = SensorCtrlType::NONE;
  ps.motion_type = MotionType::STRAIGHT;
  ps.dia_mode = false;
  mp->go_straight(ps);
  while (1) {
    vTaskDelay(1.0 / portTICK_RATE_MS);
    if (ui->button_state_hold()) {
      break;
    }
  }
  pt->motor_disable();
}
void MainTask::echo_sensing_result_with_json() {
  mp->reset_gyro_ref_with_check();
  while (1) {
    // entity_to_json(json_instance);
    // printf("%s\n", json_instance.dump().c_str());
    vTaskDelay(xDelay50);
    bool break_btn = ui->button_state_hold();
    if (break_btn) {
      ui->coin(100);
      break;
    }
  }
}
vector<string> MainTask::split(const string &s, char delim) {
  vector<string> elems;
  stringstream ss(s);
  string item;
  while (getline(ss, item, delim)) {
    if (!item.empty()) {
      elems.push_back(item);
    }
  }
  return elems;
}

void MainTask::save_json_data(std::string &str) {
  mount();
  //「ファイル名@JSON文字列」の体裁でクエリーが来ること前提
  auto res = split(str, '@'); // セパレータ「＠」で分割
  if (res.size() != 2)        // invalid check
    return;

  // mount領域+ファイル名を指定しファイルを開く
  auto tgt_file = "/spiflash/" + res[0];
  auto *f = fopen(tgt_file.c_str(), "wb");
  if (f == NULL)
    return;
  // 書き込み&ファイルclose
  fprintf(f, res[1].c_str());
  fclose(f);
  // printf("%s\n", str.c_str());
  ui->coin(25);
}

void MainTask::load_hw_param() {
  string fileName = "/spiflash/hardware.txt";

  std::ifstream ifs(fileName);
  if (!ifs) {
    return;
  }
  std::string str;
  std::string buf;
  while (!ifs.eof()) {
    std::getline(ifs, buf);
    str += buf;
  }

  // printf("%s\n", str.c_str());

  cJSON *root = cJSON_CreateObject(), *motor_pid, *motor_pid2, *motor_pid3,
        *gyro_pid, *str_agl_pid, *str_agl_dia_pid, *gyro_param, *kalman_config,
        *battery_param, *led_param, *angle_pid, *dist_pid, *sen_pid,
        *sen_pid_dia, *accel_x, *comp_v_param, *axel_degenerate_x,
        *axel_degenerate_y, *led_blight, *gyro_pid_gain_limitter,
        *motor_pid_gain_limitter, *motor2_pid_gain_limitter,
        *motor3_pid_gain_limitter;

  root = cJSON_Parse(str.c_str());

  param->dt = getItem(root, "dt")->valuedouble;
  param->tire = getItem(root, "tire")->valuedouble;
  param->tire2 = getItem(root, "tire2")->valuedouble;
  param->log_size = getItem(root, "log_size")->valueint;
  param->gear_a = getItem(root, "gear_a")->valuedouble;
  param->gear_b = getItem(root, "gear_b")->valuedouble;
  param->max_duty = getItem(root, "max_duty")->valuedouble;
  param->min_duty = getItem(root, "min_duty")->valuedouble;
  param->Ke = getItem(root, "Ke")->valuedouble;
  param->Km = getItem(root, "Km")->valuedouble;
  param->Resist = getItem(root, "Resist")->valuedouble;
  param->Mass = getItem(root, "Mass")->valuedouble;
  param->Lm = getItem(root, "Lm")->valuedouble;
  param->tire_tread = getItem(root, "tire_tread")->valuedouble;
  param->led_light_delay_cnt =
      getItem(root, "led_light_delay_cnt")->valuedouble;
  param->led_light_delay_cnt2 =
      getItem(root, "led_light_delay_cnt2")->valuedouble;
  param->search_sen_ctrl_limitter =
      getItem(root, "search_sen_ctrl_limitter")->valuedouble;
  param->ff_front_gain_14 = getItem(root, "ff_front_gain_14")->valuedouble;
  param->ff_roll_gain_before =
      getItem(root, "ff_roll_gain_before")->valuedouble;
  param->ff_roll_gain_after = getItem(root, "ff_roll_gain_after")->valuedouble;

  param->left_keep_dist_th = getItem(root, "left_keep_dist_th")->valuedouble;

  param->normal_sla_l_wall_off_th_in =
      getItem(root, "normal_sla_l_wall_off_th_in")->valueint;
  param->normal_sla_r_wall_off_th_in =
      getItem(root, "normal_sla_r_wall_off_th_in")->valueint;
  param->normal_sla_l_wall_off_th_out =
      getItem(root, "normal_sla_l_wall_off_th_out")->valueint;
  param->normal_sla_r_wall_off_th_out =
      getItem(root, "normal_sla_r_wall_off_th_out")->valueint;
  param->normal_sla_l_wall_off_ref_cnt =
      getItem(root, "normal_sla_l_wall_off_ref_cnt")->valueint;
  param->normal_sla_r_wall_off_ref_cnt =
      getItem(root, "normal_sla_r_wall_off_ref_cnt")->valueint;
  param->normal_sla_l_wall_off_dist =
      getItem(root, "normal_sla_l_wall_off_dist")->valueint;
  param->normal_sla_r_wall_off_dist =
      getItem(root, "normal_sla_r_wall_off_dist")->valueint;
  param->normal_sla_l_wall_off_margin =
      getItem(root, "normal_sla_l_wall_off_margin")->valueint;
  param->normal_sla_r_wall_off_margin =
      getItem(root, "normal_sla_r_wall_off_margin")->valueint;

  const unsigned long motor_hz = getItem(root, "MotorHz")->valueint;
  const unsigned long suction_motor_hz = getItem(root, "SuctionHz")->valueint;
  const unsigned long motor_res = getItem(root, "MotorResolution")->valueint;
  const unsigned long suction_motor_res =
      getItem(root, "SuctionResolution")->valueint;
  pt->set_motor_hz(motor_hz, motor_res);
  pt->set_suction_motor_hz(suction_motor_hz, suction_motor_res);

  param->Lm = getItem(root, "Lm")->valuedouble;
  param->slip_param_K = getItem(root, "slip_param_K")->valuedouble;
  param->slip_param_k2 = getItem(root, "slip_param_k2")->valuedouble;
  param->sen_log_size = getItem(root, "sen_log_size")->valueint;
  param->offset_start_dist = getItem(root, "offset_start_dist")->valuedouble;
  param->offset_start_dist_search =
      getItem(root, "offset_start_dist_search")->valuedouble;
  param->sakiyomi_time = getItem(root, "sakiyomi_time")->valuedouble;

  axel_degenerate_x = getItem(root, "axel_degenerate_x");
  axel_degenerate_y = getItem(root, "axel_degenerate_y");
  int list_size = cJSON_GetArraySize(axel_degenerate_x);
  for (int i = 0; i < list_size; i++) {
    const auto x = cJSON_GetArrayItem(axel_degenerate_x, i)->valuedouble;
    const auto y = cJSON_GetArrayItem(axel_degenerate_y, i)->valuedouble;
    pt->axel_degenerate_x.emplace_back(x);
    pt->axel_degenerate_y.emplace_back(y);
  }

  led_blight = getItem(root, "led_blight");
  int list_size2 = cJSON_GetArraySize(led_blight);
  ui->blight_level_list.clear();
  for (int i = 0; i < list_size2; i++) {
    const uint8_t level = cJSON_GetArrayItem(led_blight, i)->valueint;
    ui->blight_level_list.emplace_back(level);
  }

  param->ff_v_th = getItem(root, "ff_v_th")->valuedouble;
  param->ff_front_dury = getItem(root, "ff_front_dury")->valuedouble;

  param->fail_check.duty = getItem(root, "fail_duty_cnt")->valueint;
  param->fail_check.v = getItem(root, "fail_v_cnt")->valueint;
  param->fail_check.w = getItem(root, "fail_w_cnt")->valueint;
  param->fail_check.ang = getItem(root, "fail_ang_cnt")->valueint;
  param->fail_check.wall_off = getItem(root, "fail_wall_off_cnt")->valueint;
  tgt_val->ego_in.ff_duty_low_th = param->ff_front_dury;
  tgt_val->ego_in.ff_duty_low_v_th = param->ff_v_th;
  param->front_ctrl_error_th =
      getItem(root, "front_ctrl_error_th")->valuedouble;

  param->logging_time =
      getItem(root, "logging_time")->valuedouble / portTICK_PERIOD_MS;
  param->set_param = true;

  param->search_log_enable = getItem(root, "search_log_enable")->valueint;
  param->test_log_enable = getItem(root, "test_log_enable")->valueint;
  param->fast_log_enable = getItem(root, "fast_log_enable")->valueint;

  param->FF_front = getItem(root, "FF_front")->valueint;
  param->FF_roll = getItem(root, "FF_roll")->valueint;
  param->FF_keV = getItem(root, "FF_keV")->valueint;

  motor_pid = getItem(root, "motor_pid");
  param->motor_pid.p = getItem(motor_pid, "p")->valuedouble;
  param->motor_pid.i = getItem(motor_pid, "i")->valuedouble;
  param->motor_pid.d = getItem(motor_pid, "d")->valuedouble;
  param->motor_pid.b = getItem(motor_pid, "b")->valuedouble;
  param->motor_pid.c = getItem(motor_pid, "c")->valuedouble;
  param->motor_pid.mode = getItem(motor_pid, "mode")->valueint;

  motor_pid_gain_limitter = getItem(root, "motor_pid_gain_limitter");
  param->motor_pid_gain_limitter.p =
      getItem(motor_pid_gain_limitter, "p")->valuedouble;
  param->motor_pid_gain_limitter.i =
      getItem(motor_pid_gain_limitter, "i")->valuedouble;
  param->motor_pid_gain_limitter.d =
      getItem(motor_pid_gain_limitter, "d")->valuedouble;
  param->motor_pid_gain_limitter.b =
      getItem(motor_pid_gain_limitter, "b")->valuedouble;
  param->motor_pid_gain_limitter.c =
      getItem(motor_pid_gain_limitter, "c")->valuedouble;
  param->motor_pid_gain_limitter.mode =
      getItem(motor_pid_gain_limitter, "mode")->valueint;

  motor2_pid_gain_limitter = getItem(root, "motor2_pid_gain_limitter");
  param->motor2_pid_gain_limitter.p =
      getItem(motor2_pid_gain_limitter, "p")->valuedouble;
  param->motor2_pid_gain_limitter.i =
      getItem(motor2_pid_gain_limitter, "i")->valuedouble;
  param->motor2_pid_gain_limitter.d =
      getItem(motor2_pid_gain_limitter, "d")->valuedouble;
  param->motor2_pid_gain_limitter.b =
      getItem(motor2_pid_gain_limitter, "b")->valuedouble;
  param->motor2_pid_gain_limitter.c =
      getItem(motor2_pid_gain_limitter, "c")->valuedouble;
  param->motor2_pid_gain_limitter.mode =
      getItem(motor2_pid_gain_limitter, "mode")->valueint;

  motor3_pid_gain_limitter = getItem(root, "motor3_pid_gain_limitter");
  param->motor3_pid_gain_limitter.p =
      getItem(motor3_pid_gain_limitter, "p")->valuedouble;
  param->motor3_pid_gain_limitter.i =
      getItem(motor3_pid_gain_limitter, "i")->valuedouble;
  param->motor3_pid_gain_limitter.d =
      getItem(motor3_pid_gain_limitter, "d")->valuedouble;
  param->motor3_pid_gain_limitter.b =
      getItem(motor3_pid_gain_limitter, "b")->valuedouble;
  param->motor3_pid_gain_limitter.c =
      getItem(motor3_pid_gain_limitter, "c")->valuedouble;
  param->motor3_pid_gain_limitter.mode =
      getItem(motor3_pid_gain_limitter, "mode")->valueint;

  gyro_pid_gain_limitter = getItem(root, "gyro_pid_gain_limitter");
  param->gyro_pid_gain_limitter.p =
      getItem(gyro_pid_gain_limitter, "p")->valuedouble;
  param->gyro_pid_gain_limitter.i =
      getItem(gyro_pid_gain_limitter, "i")->valuedouble;
  param->gyro_pid_gain_limitter.d =
      getItem(gyro_pid_gain_limitter, "d")->valuedouble;
  param->gyro_pid_gain_limitter.b =
      getItem(gyro_pid_gain_limitter, "b")->valuedouble;
  param->gyro_pid_gain_limitter.c =
      getItem(gyro_pid_gain_limitter, "c")->valuedouble;
  param->gyro_pid_gain_limitter.mode =
      getItem(gyro_pid_gain_limitter, "mode")->valueint;

  str_agl_pid = getItem(root, "str_agl_pid");
  param->str_ang_pid.p = getItem(str_agl_pid, "p")->valuedouble;
  param->str_ang_pid.i = getItem(str_agl_pid, "i")->valuedouble;
  param->str_ang_pid.d = getItem(str_agl_pid, "d")->valuedouble;
  param->str_ang_pid.b = getItem(str_agl_pid, "b")->valuedouble;
  param->str_ang_pid.c = getItem(str_agl_pid, "c")->valuedouble;
  param->str_ang_pid.mode = getItem(str_agl_pid, "mode")->valueint;

  str_agl_dia_pid = getItem(root, "str_agl_dia_pid");
  param->str_ang_dia_pid.p = getItem(str_agl_dia_pid, "p")->valuedouble;
  param->str_ang_dia_pid.i = getItem(str_agl_dia_pid, "i")->valuedouble;
  param->str_ang_dia_pid.d = getItem(str_agl_dia_pid, "d")->valuedouble;
  param->str_ang_dia_pid.b = getItem(str_agl_dia_pid, "b")->valuedouble;
  param->str_ang_dia_pid.c = getItem(str_agl_dia_pid, "c")->valuedouble;
  param->str_ang_dia_pid.mode = getItem(str_agl_dia_pid, "mode")->valueint;

  motor_pid2 = getItem(root, "motor_pid2");
  param->motor_pid2.p = getItem(motor_pid2, "p")->valuedouble;
  param->motor_pid2.i = getItem(motor_pid2, "i")->valuedouble;
  param->motor_pid2.d = getItem(motor_pid2, "d")->valuedouble;
  param->motor_pid2.b = getItem(motor_pid2, "b")->valuedouble;
  param->motor_pid2.c = getItem(motor_pid2, "c")->valuedouble;
  param->motor_pid2.mode = getItem(motor_pid2, "mode")->valueint;

  motor_pid3 = getItem(root, "motor_pid3");
  param->motor_pid3.p = getItem(motor_pid3, "p")->valuedouble;
  param->motor_pid3.i = getItem(motor_pid3, "i")->valuedouble;
  param->motor_pid3.d = getItem(motor_pid3, "d")->valuedouble;
  param->motor_pid3.b = getItem(motor_pid3, "b")->valuedouble;
  param->motor_pid3.c = getItem(motor_pid3, "c")->valuedouble;
  param->motor_pid3.mode = getItem(motor_pid3, "mode")->valueint;

  sen_pid = getItem(root, "sensor_pid");
  param->sensor_pid.p = getItem(sen_pid, "p")->valuedouble;
  param->sensor_pid.i = getItem(sen_pid, "i")->valuedouble;
  param->sensor_pid.d = getItem(sen_pid, "d")->valuedouble;
  param->sensor_pid.b = getItem(sen_pid, "b")->valuedouble;
  param->sensor_pid.mode = getItem(sen_pid, "mode")->valueint;

  sen_pid_dia = getItem(root, "sensor_pid_dia");
  param->sensor_pid_dia.p = getItem(sen_pid_dia, "p")->valuedouble;
  param->sensor_pid_dia.i = getItem(sen_pid_dia, "i")->valuedouble;
  param->sensor_pid_dia.d = getItem(sen_pid_dia, "d")->valuedouble;
  param->sensor_pid_dia.mode = getItem(sen_pid_dia, "mode")->valueint;
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

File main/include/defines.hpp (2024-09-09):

#ifndef DEFINES_HPP
#define DEFINES_HPP

#include "driver/gpio.h"
#include "driver/ledc.h"
#include "gen_code_mpc/bus.h"
#include "include/maze_solver.hpp"
#include "sdkconfig.h"
#include "soc/adc_channel.h"
#include "soc/gpio_struct.h"
#include "soc/ledc_periph.h"

#include "fs.hpp"
#include "include/enums.hpp"
#include "include/structs.hpp"
#include "sdkconfig.h"
#include <bitset>
#include <initializer_list>
#include <iostream>
#include <memory>
#include <sstream>
#include <string>
#include <string_view>
#include <unordered_map>
#include <vector>

#include "esp_heap_caps.h"
#include "icm20689.hpp"
#include "lsm6dsr.hpp"

#define portTICK_RATE_MS portTICK_PERIOD_MS
#define xTaskHandle TaskHandle_t

#define ABS(IN) ((IN) < 0 ? -(IN) : (IN))

constexpr int GY_DQ_SIZE = 2;
constexpr int GY_CYCLE = 2500; // 2500=1/4msec
// constexpr int GY_CYCLE = 1250; // 1250=1/8msec
constexpr int GY_MODE = 0;
constexpr float cell_size = 90;

constexpr gpio_num_t SDA_PIN = GPIO_NUM_16;
constexpr gpio_num_t SCL_PIN = GPIO_NUM_14;

constexpr gpio_num_t LED_EN = GPIO_NUM_10;
constexpr gpio_num_t LED_A0 = GPIO_NUM_11;
constexpr gpio_num_t LED_A1 = GPIO_NUM_12;

constexpr gpio_num_t TXD = GPIO_NUM_43;
constexpr gpio_num_t RXD = GPIO_NUM_44;
constexpr gpio_num_t RTS = GPIO_NUM_15;
constexpr gpio_num_t CTS = GPIO_NUM_16;

constexpr gpio_num_t L_CW_CCW1 = GPIO_NUM_39;
constexpr gpio_num_t L_CW_CCW2 = GPIO_NUM_40;
constexpr gpio_num_t R_CW_CCW1 = GPIO_NUM_41;
constexpr gpio_num_t R_CW_CCW2 = GPIO_NUM_42;

constexpr uint32_t L_CW_CCW1_BIT = BIT(GPIO_NUM_39 - 32);
constexpr uint32_t L_CW_CCW2_BIT = BIT(GPIO_NUM_40 - 32);
constexpr uint32_t R_CW_CCW1_BIT = BIT(GPIO_NUM_41 - 32);
constexpr uint32_t R_CW_CCW2_BIT = BIT(GPIO_NUM_42 - 32);

constexpr gpio_num_t Motor_L_PWM = GPIO_NUM_38;
constexpr gpio_num_t Motor_L_PWM2 = GPIO_NUM_38;
constexpr gpio_num_t Motor_R_PWM = GPIO_NUM_46;
constexpr gpio_num_t Motor_R_PWM2 = GPIO_NUM_46;

constexpr gpio_num_t BUZZER = GPIO_NUM_5;

constexpr gpio_num_t SW1 = GPIO_NUM_34;

constexpr gpio_num_t EN_MISO = GPIO_NUM_1;
constexpr gpio_num_t EN_MOSI = GPIO_NUM_2;
constexpr gpio_num_t EN_CLK = GPIO_NUM_3;
constexpr gpio_num_t EN_GN_SSL = GPIO_NUM_4;

constexpr gpio_num_t ENC_R_CS = GPIO_NUM_6;
constexpr gpio_num_t ENC_L_CS = GPIO_NUM_37;
constexpr gpio_num_t ENC_CLK = GPIO_NUM_7;
constexpr gpio_num_t ENC_MISO = GPIO_NUM_8; // B
constexpr gpio_num_t ENC_MOSI = GPIO_NUM_9; // A

constexpr gpio_num_t SUCTION_PWM = GPIO_NUM_35;

#define SEN_R90 ADC2_CHANNEL_2
#define SEN_L90 ADC2_CHANNEL_4
#define SEN_R45 ADC2_CHANNEL_6
#define SEN_L45 ADC2_CHANNEL_7
#define BATTERY ADC2_CHANNEL_9

#define SEN_R90_GPIO GPIO_NUM_13
#define SEN_L90_GPIO GPIO_NUM_15
#define SEN_R45_GPIO GPIO_NUM_17
#define SEN_L45_GPIO GPIO_NUM_18
#define BATTERY_GPIO GPIO_NUM_20

#define MAX(a, b) ((a) > (b) ? (a) : (b))
#define MIN(a, b) ((a) < (b) ? (a) : (b))

// constexpr adc2_channel_t SEN_R90 = ADC2_CHANNEL_0;
// constexpr adc2_channel_t SEN_R45 = ADC2_CHANNEL_1;
// constexpr adc2_channel_t SEN_F = ADC2_CHANNEL_4;
// constexpr adc2_channel_t SEN_L45 = ADC2_CHANNEL_6;
// constexpr adc2_channel_t SEN_L90 = ADC2_CHANNEL_8;
// constexpr adc2_channel_t BATTERY = ADC2_CHANNEL_9;

constexpr int16_t ENCODER_H_LIM_VAL = 32767;
constexpr int16_t ENCODER_L_LIM_VAL = -32767;

const int16_t ENC_RESOLUTION = 16384 - 1;
constexpr uint8_t READ_FLAG = 0x80;
constexpr uint16_t READ_FLAG2 = 0b01000000;
constexpr uint16_t PARITY_FLAG = 0b10000000;
constexpr uint8_t ESC = 0x1B;
constexpr uint16_t BUF_SIZE = 4096;

constexpr uint16_t MOTION_CHECK_TH = 1000;
constexpr uint16_t ENC_OPE_V_R_TH = 175;

constexpr uint16_t LOG_SIZE = 1300;
constexpr uint16_t LINE_BUF_SIZE = 1024;
// constexpr float BATTERY_GAIN = 3.2075; // 2.97324;
constexpr float BATTERY_GAIN = 3.317057486323464; // 2.97324;

constexpr uint8_t LEDC_HIGH_SPEED_MODE = 0;
constexpr float LOW_BATTERY_TH = 11.7;

constexpr uint16_t RESET_GYRO_LOOP_CNT = 512;

static const std::string slalom_log_file("/spiflash/sla.log");
static const std::string sysid_log_file("/spiflash/sysid.log");
static const std::string maze_log_file("/spiflash/maze.txt");
static const std::string maze_log_kata_file("/spiflash/maze_kata.log");
static const std::string maze_log_return_file("/spiflash/maze_return.log");
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

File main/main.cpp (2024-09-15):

#include "driver/adc.h"
#include "driver/gpio.h"
#include "driver/ledc.h"
#include "driver/mcpwm.h"
#include "driver/pcnt.h"
#include "driver/spi_common.h"
#include "driver/spi_master.h"
#include "driver/timer.h"
#include "driver/uart.h"
#include "esp_adc_cal.h"
#include "freertos/FreeRTOS.h"
#include "freertos/task.h"
#include "include/adachi.hpp"
#include "include/defines.hpp"
#include "include/sensing.hpp"
#include "sdkconfig.h"
#include "soc/adc_channel.h"
#include "soc/ledc_periph.h"
#include "xtensa/core-macros.h"
#include <driver/adc.h>
#include <esp_adc_cal.h>
#include <esp_task_wdt.h>
#include <stdio.h>
#include <stdlib.h>
#include <string.h>
// #include "VL53L0X.h"
// #include "esp_efuse_rtc_calib.h"

#include "include/logging_task.hpp"
#include "include/main_task.hpp"
#include "include/planning_task.hpp"
#include "include/sensing_task.hpp"

#include "esp_system.h"
#include "esp_vfs.h"
#include "esp_vfs_fat.h"

#include <iostream>
#include <sstream>
#include <string>
#include <vector>

#include "esp_debug_helpers.h"
#include "rom/uart.h"

#include "freertos/FreeRTOS.h"
#include "freertos/queue.h"
#include "freertos/task.h"

#include <eigen3/Eigen/Eigen>

// #include <Eigen/Core>

void init_uart() {
  uart_config_t uart_config;
  uart_config.baud_rate = 3 * 1000 * 1000;
  uart_config.data_bits = UART_DATA_8_BITS;
  uart_config.parity = UART_PARITY_DISABLE;
  uart_config.stop_bits = UART_STOP_BITS_1;
  uart_config.flow_ctrl = UART_HW_FLOWCTRL_DISABLE;
  // uart_config.rx_flow_ctrl_thresh = 122;
  uart_config.source_clk = UART_SCLK_APB;
  int intr_alloc_flags = 0;
  uart_param_config(UART_NUM_0, &uart_config);
  uart_driver_install(UART_NUM_0, BUF_SIZE * 2, 0, 0, NULL, intr_alloc_flags);
  uart_param_config(UART_NUM_0, &uart_config);
  uart_set_pin(UART_NUM_0, TXD, RXD, RTS, CTS);
}

void init_gpio() {
  gpio_config_t io_conf;
  // 割り込みをしない
  io_conf.intr_type = GPIO_INTR_DISABLE;
  // 出力モード
  io_conf.mode = GPIO_MODE_OUTPUT;
  // 設定したいピンのビットマスク
  io_conf.pin_bit_mask = 0;
  // io_conf.pin_bit_mask |= 1ULL << LED_R90;
  // io_conf.pin_bit_mask |= 1ULL << LED_R45;
  // io_conf.pin_bit_mask |= 1ULL << LED_L45;
  // io_conf.pin_bit_mask |= 1ULL << LED_L90;
  io_conf.pin_bit_mask |= 1ULL << LED_A0;
  io_conf.pin_bit_mask |= 1ULL << LED_A1;
  io_conf.pin_bit_mask |= 1ULL << LED_EN;

  io_conf.pin_bit_mask |= 1ULL << L_CW_CCW1;
  io_conf.pin_bit_mask |= 1ULL << R_CW_CCW1;
  io_conf.pin_bit_mask |= 1ULL << SUCTION_PWM;

  io_conf.pin_bit_mask |= 1ULL << Motor_L_PWM;
  io_conf.pin_bit_mask |= 1ULL << Motor_R_PWM;

  // io_conf.pin_bit_mask |= 1ULL << LED1;
  // io_conf.pin_bit_mask |= 1ULL << LED2;
  // io_conf.pin_bit_mask |= 1ULL << LED3;
  // io_conf.pin_bit_mask |= 1ULL << LED4;
  // io_conf.pin_bit_mask |= 1ULL << LED5;

  io_conf.pin_bit_mask |= 1ULL << BUZZER;

  // io_conf.pin_bit_mask |= 1ULL << SUCTION_PWM;

  // 内部プルダウンしない
  io_conf.pull_down_en = (gpio_pulldown_t)0;
  // 内部プルアップしない
  io_conf.pull_up_en = (gpio_pullup_t)0;
  // 設定をセットする
  gpio_config(&io_conf);
  gpio_set_level(SUCTION_PWM, 0);
  // gpio_set_direction((gpio_num_t)GPIO_OUTPUT_IO_8,
}

DRAM_ATTR std::shared_ptr<input_param_t> param =
    std::make_shared<input_param_t>();
DRAM_ATTR std::shared_ptr<sensing_result_entity_t> sensing_entity =
    std::make_shared<sensing_result_entity_t>();
DRAM_ATTR std::shared_ptr<motion_tgt_val_t> tgt_val =
    std::make_shared<motion_tgt_val_t>();
DRAM_ATTR std::shared_ptr<pid_error_entity_t> error_entity =
    std::make_shared<pid_error_entity_t>();
DRAM_ATTR std::shared_ptr<PlanningTask> pt = std::make_shared<PlanningTask>();
DRAM_ATTR std::shared_ptr<LoggingTask> lt = std::make_shared<LoggingTask>();
DRAM_ATTR std::shared_ptr<MainTask> mt = std::make_shared<MainTask>();
DRAM_ATTR std::shared_ptr<SensingTask> st = std::make_shared<SensingTask>();
// std::shared_ptr<Sensing> sn = std::make_shared<Sensing>();
TaskHandle_t xTaskHandler;
// SensingTask st;

std::shared_ptr<sensing_result_entity_t> get_sensing_entity() {
  return sensing_entity;
}
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

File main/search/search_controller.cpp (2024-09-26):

#include "include/search_controller.hpp"

SearchController::SearchController() {
  adachi = std::make_shared<Adachi>();
  ego = std::make_shared<ego_t>();
  adachi->set_ego(ego);
}
SearchController::~SearchController() {}

void SearchController::set_lgc(std::shared_ptr<MazeSolverBaseLgc> &_lgc) {
  lgc = _lgc;
  adachi->set_logic(_lgc);
  lgc->set_ego(ego);
}

void SearchController::set_motion_plannning(
    std::shared_ptr<MotionPlanning> &_mp) {
  mp = _mp;
}

void SearchController::set_planning_task(std::shared_ptr<PlanningTask> &_pt) {
  pt = _pt;
}

void SearchController::set_sensing_entity(
    std::shared_ptr<sensing_result_entity_t> &_entity) {
  sensing_result = _entity;
}

void SearchController::set_logging_task(std::shared_ptr<LoggingTask> &_lt) {
  lt = _lt;
}

void SearchController::set_userinterface(std::shared_ptr<UserInterface> &_ui) {
  ui = _ui;
}
void SearchController::reset() {
  ego->dir = Direction::North;
  ego->x = 0;
  ego->y = 1;
  ego->prev_motion = 0; // not use
  lgc->set_default_wall_data();
  adachi->reset_goal();
}
MotionResult SearchController::go_straight_wrapper(param_set_t &p_set,
                                                   float diff,
                                                   StraightType st) {
  // param_straight_t p;
  p.v_max = p_set.str_map[st].v_max;
  if (p.v_max + 10 < pt->mpc_next_ego.v) {
    p.v_max = p_set.str_map[StraightType::FastRun].v_max;
  }
  p.v_end = p_set.str_map[st].v_max;
  if (st == StraightType::FastRunDia) {
    p.v_end = p_set.str_map[StraightType::Search].v_max;
  }

  p.accl = p_set.str_map[st].accl;
  p.decel = p_set.str_map[st].decel;

  p.dist = param->cell - diff;
  p.motion_type = MotionType::STRAIGHT;
  p.wall_off_req = WallOffReq::NONE;
  p.sct = SensorCtrlType::Straight;
  p.wall_off_dist_r = param->sen_ref_p.search_exist.offset_r;
  p.wall_off_dist_l = param->sen_ref_p.search_exist.offset_l;
  p.dia_mode = false;
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

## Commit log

2023-03-25 cp Exia7th
    [hardware.yaml]
2023-06-12 sensing_taskをRTOSから離脱
2023-08-01 add 調整手順
2023-08-01 update param
    [hardware.yaml]
2023-08-01 update 区画中心調整
2023-08-01 update 前壁制御調整
2023-09-08 feat: kanazawa
    [hardware.yaml]
2023-09-18 2023.09.10 kanazawa
    [hardware.yaml]
2023-11-26 update for BansheeAlter
    [hardware.yaml]
2023-12-09 feat: pid gain plot
    [hardware.yaml]
2023-12-13 feat: add classic mode
    [hardware.yaml]
2024-02-11 update chubu
    [hardware.yaml]
2024-02-16 update: readme
    [Banshee.brd, BansheeNornV5.brd, BansheeNornV5.sch]
2024-09-17 update 0917
    [hardware.yaml]
2024-09-19 update params
    [hardware.yaml]
2024-09-26 update for hokushinetsu
    [hardware.yaml]
